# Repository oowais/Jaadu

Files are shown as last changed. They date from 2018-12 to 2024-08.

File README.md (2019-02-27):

# Jaadu : the Alien in FabTerrarium

A **FabTerrarium** is a space with different animals/plants which can interact with users or other entities within the terrarium. These animals/plants are either 3D prninted or soft-robots or a combination of both.

**Jaadu** is an alien in the FabTerrarium who is curious about the different animals or plants in the space. It is a small toddler who crawls in the terrarium reading the emotions of the other entities and displaying those emotions in itself.

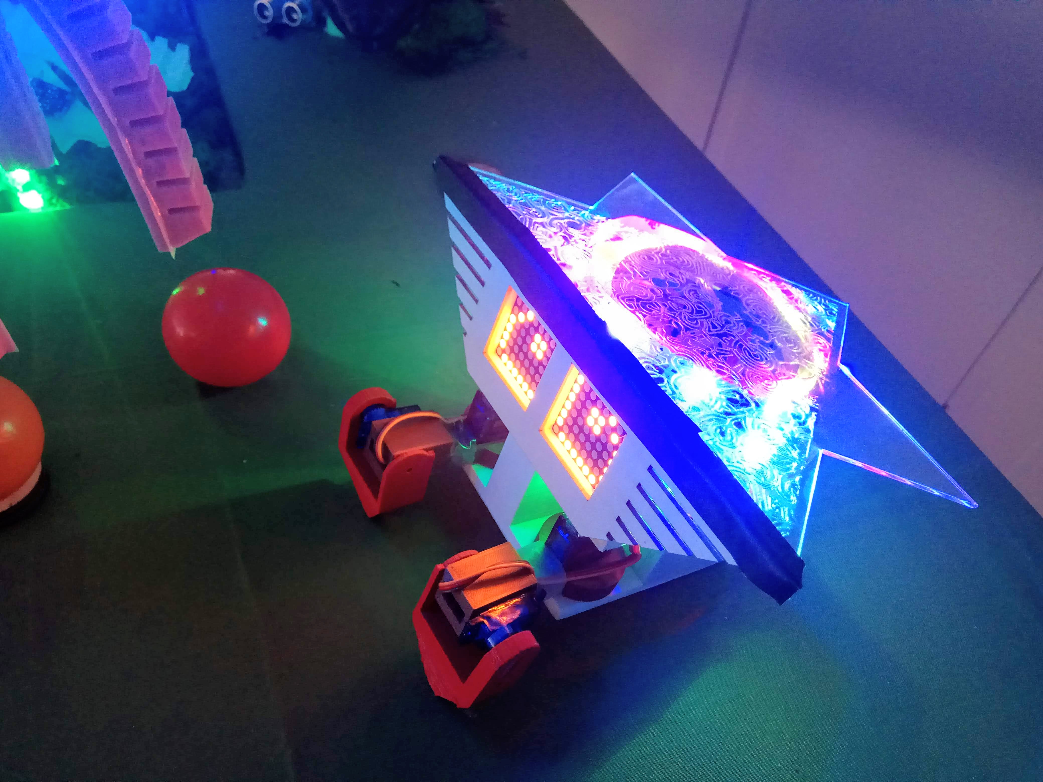
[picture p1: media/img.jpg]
Jaadu


**PowerHand** is the movement controller for the Alien. Moving it around triggers the Alien to move.

**Emotion Gateways** are the gateways placed in the Terrarium through which the Alien can pick up emotions of other entities.

Read more at our [blog](https://students.hci.rwth-aachen.de/category/ws1819/mcp-ws1819-group2) on the project and how it came to be.

## Repo Details

* **alien** : Contains the code for the Alien.
* **backdoor** : Contains the client side code for communicating with the backdoor over MQTT.
* **ground** : Contains the code for synchronization between the Emotion Gateways and sending the triggers in the ground to the Alien.
* **media** : Different images/videos used in the repo.
* **models** : All models designed for laser cutting or 3D printing, some discarded and some used.
* **powerhand** : Code for control of LEDs and triggers sent to Alien in the PowerHand.
* **scripts** : Contains scripts used in the project.
* **testing_modules** : Testing codes and information.

## Items used

* **Alien :**
  * RasPI Zero W
  * Adafruit RGB LED Strip
  * Adafruit LED 8x8 Matrix (2)
  * TowerPro SG90 Servo (4)
* **PowerHand :**
  * Arduino Nano
  * Accelerometer
  * HC-05 Bluetooth Module
  * Adafruit RGB LED Strip
* **Ground :**
  * Arduno Uno
  * HC-05 Bluetooth Module
  * HC-SR04 Ultrasonic Sensor (2)
  * Adafruit RGB LED Strip (2)
* **Additionally :**
  * Finnappee
  * PlexiGlas
  * PLA
  * Breadboard
  * Jumper Cables
  * Tapes
  * Loads and loads of Glue

# Thoughts on looking back

* The walking mechanism developed which relies on the Servos is not suitable to be driven by a RasPI. The Servos by TowerPro are not really reliable and go bust often. A better and reliable mechanism is needed.
* Bluetooth HC-05 module keeps disconnecting after some time, not reliable.
* RaspPi Zero W with it's single core is not a good driver for 7 threads. Things get real slow real quick. RasPI 3 might be a better alternative.
* PowerHand doesn't have proper signifiers for how to use it. Design could be better.
* Power requirements for the LED Matrix, LED Strip is quite high. A 1.5A current (given out usually a small powerbank) is not sufficient. A smaller, light-weight and higher output current power source should be thought of.

---

The **Interactive FabTerrarium** project was conducted as the **Media Computing Project** by the [Media Computing Group](https://hci.rwth-aachen.de/) group under [RWTH Aachen](http://www.rwth-aachen.de).

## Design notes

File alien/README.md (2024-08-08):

# Alien

The central controller for all the different individual components inside the Alien.

## Wiring

**Note :** Servos are driven by external power (RasPI can't bear the load). All VCC and GND for Servos need to be connected to the external source. External power source GND also has to be connected with RasPI GND.

<table>
  <tr>
    <th> Connection </th><th> Right </th><th> RasPI Zero W Board </th><th> Left </th><th> Connection </th>
  </tr>
  <tr>
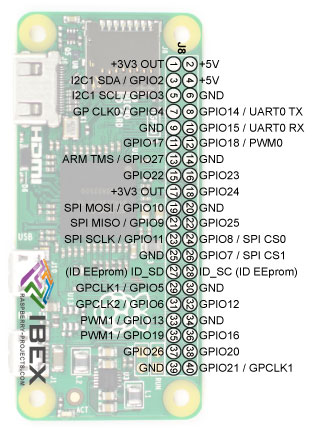
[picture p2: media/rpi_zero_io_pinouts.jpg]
    <td></td><td>1</td><td rowspan=20>  </td> <td>2</td><td>VCC OUT</td>
  </tr>
  <tr>
    <td>Left Eye SDA</td><td>3</td><td>4</td><td></td>
  </tr>
  <tr>
    <td>Left Eye SCL</td><td>5</td><td>6</td><td>GND OUT</td>
  </tr>
  <tr>
    <td></td><td>7</td><td>8</td><td></td>
  </tr>
  <tr>
    <td></td><td>9</td><td>10</td><td></td>
  </tr>
  <tr>
    <td></td><td>11</td><td>12</td><td>LED DOUT</td>
  </tr>
  <tr>
    <td></td><td>13</td><td>14</td><td></td>
  </tr>
  <tr>
    <td></td><td>15</td><td>16</td><td>Right Eye SDA</td>
  </tr>
  <tr>
    <td></td><td>17</td><td>18</td><td>Right Eye SCL</td>
  </tr>
  <tr>
    <td></td><td>19</td><td>20</td><td></td>
  </tr>
  <tr>
    <td></td><td>21</td><td>22</td><td>Right Leg CTRL</td>
  </tr>
  <tr>
    <td></td><td>23</td><td>24</td><td></td>
  </tr>
  <tr>
    <td>GND for External Power</td><td>25</td><td>26</td><td></td>
  </tr>
  <tr>
    <td></td><td>27</td><td>28</td><td></td>
  </tr>
  <tr>
    <td></td><td>29</td><td>30</td><td>GND OUT</td>
  </tr>
  <tr>
    <td></td><td>31</td><td>32</td><td></td>
  </tr>
  <tr>
    <td></td><td>33</td><td>34</td><td></td>
  </tr>
  <tr>
    <td></td><td>35</td><td>36</td><td>Left Leg CTRL</td>
  </tr>
  <tr>
    <td>Right Foot CTRL</td><td>37</td><td>38</td><td>Left Foot CTRL</td>
  </tr>
  <tr>
    <td></td><td>39</td><td>40</td><td></td>
  </tr>
</table>

## Installation

Run the [script](../scripts/) to complete installation of the alien package inside RasPI.
Starts the Alien program automatically as a service on the RasPI.

## Some things to take care

Changes in **lib/globals.py** :

* **EXTERNAL_BROKER_HOST** needs to point to the IP address of the MQTT Broker.
* **EXTERNAL_BROKER_PORT** needs to be changed if the Broker listens at a different port (1883 is default)
* **WALKING_PINS** are RasPI GPIO pin numbers and need to be changed if the connection is made different from as given.
* **MOVE_CONTROL_VALUES** are experimental values. The exact values change depending on how the Alien legs are screwed in.
Experiments can be done using [this](../testing_modules/pigpio_test/servo_demo.py).
* **WALKING_PINS** has GPIO pin numbers. Need to be changed if using different connection.
* **HAND_BLUETOOTH_MAC** according to the MAC of the powerhand Bluetooth device.
* **GROUND_BLUETOOTH_MAC** according to the MAC of the ground connected Bluetooth device.
* **LED_STRIP_PIN** is the GPIO pin number. Change if using different connections.
* **NUM_PIXELS_USED** change according to number of LEDs in the strip used in Alien.

Changes in **mqtt_topic_mappings.json** :

Change the topic on which the emotions are sent by the other entities in the terrarium and unique key we will be using to track those emotions.

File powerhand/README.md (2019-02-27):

## Powerhand

**PowerHand** is the movement controller for the Jaadu. Moving it around triggers the Jaadu to move.

By pressing the button and moving the the powerhand in specific directions, can move Jaadu forward, left and right. Using a gesture via powerhand Jaadu can also say Hi.

[Link to demo video](https://www.youtube.com/watch?v=woAhQqzkfWM)

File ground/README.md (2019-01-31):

# Ground Controller

Arduino code used to receive triggers from the Gateways and signal via Bluetooth to the main Alien. The Alien receives the trigger and translates the emotion for the entity in the terrarium corresponding to the Gateway.

Each Gateway has a __LED Strip__ (breathing lights showing Gateway state) and an __UltraSonic sensor__.

## Wiring
* As defined in the [code](./ground.ino)
* For Bluetooth :
  * RX (on bluetooth) :arrow_right: tx_conn (on Arduino)
  * TX (on bluetooth) :arrow_right: rx_conn (on Arduino)
  * VCC connected to 3.3V OUT.

## Gateway States

* __Neutral :__ None of the Gateways are activated. LED Strips display BLUE color.
* __Activated :__  The UltraSonic sensor is triggered when some obstruction is detected in front of the gateway. (10-16 cms range). The LED Strips corresponding to the Gateway turn into GREEN color.
* __Deactivated :__ When one gateway is activated, others are in this state and doesn't trigger even when some object comes in the activation range. The LED Strips corresponding to the Gateway display RED color.

## Before Using

* If Pins used are different than given then have to change the corresponding pin numbers in **ground.ino**
* Each Gateway instance needs a separate character to be provided as uniqueID. These characters should correspond to triggers in the [receiver code](../alien/lib/ground_coordinator.py)

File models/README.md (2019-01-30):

# Models

All the STL (for 3D printing) and SVG (for Laser cutting) files developed for the project.

## Alien

* **arm_left :** Left Leg for the Alien
* **arm_right :** Right Leg for the Alien
* **backmost_hold :** A back stand for the alien, although we ended up making it using plexiglas which can be found in the backmost_glass.
* **base :** The complete base on which the other components are glued in. Contains holes to fit the Alien Legs.
* **finishing :** Some finishing parts for the Alien. Like the Face mask, the top gear of the Alien.
* **front :** The eye sockets for the Alien's face.
* **leg_left :** Left foot for the Alien.
* **leg_right :** Right foot for the Alien.
* **rasp_case :** A case to keep the RasPI (not really required, can be removed or better to screw in RasPI).
* **body :** The complete Alien look for visualization purpose. (without the finishing)

## Ground

* **middle_part :** The middle hold for the Gateway. Around the curved stripes LED strips are put.
* **sonar_cut :** A piece of material, which is used for the decoration of the UltraSonic sensor.
* **talk_points :** The complete gateway assembled look for visualization.

## Powerhand

* **battery_holder :** Hollow case for holding a standard sized 9V barrel battery.
* **button_holder :** To hide exposed wires going from button. button_holder_1 not really useful.
* **extension_holder :** The holder to insert the extensions in.
* **extension :** Extensions which are used for decorative purpose.
* **powerhand :** The complete powerhand assembled look for visualization.

## Discarded

A lot of models went through different design phases in the DIA cycle.
Many were discarded either due to lack of usability or not suited for our end product.
All these models dumps are available here, although they are not ordered or maintained in a proper fashion.

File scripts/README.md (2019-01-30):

# One-click setup

Script to completely setup a vanilla RasPI to run the codebase.

**Note :** Written for **Raspbian Stretch Lite (version November 2018)**.

#### Before using

* Make sure there is active internet connection in the RasPI
* Connect the Eyes (LED Matrix) to the proper pins in the RasPI since the I2C address is fetched by the script.
If eye is not connected, update the I2C address later by doing the following :
  * `i2cdetect -y 1`
  * Get the address displayed in the Matrix. If address is 0x70 nothing more needs to be done.
  * If address is something else, modify EYE_I2C_ADDRESS in [globals.py](../alien/lib/globals.py)
* If you wish to use backdoor, the set it up when asked by the script. Know more about backdoor [here](../backdoor/)

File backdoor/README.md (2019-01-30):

# Alien Backdoor

A direct secure command stream between Alien and an admin. Can be used to remotely trigger event-based triggers manually.

To be used for demo purposes (only) or to play God with the Alien (maybe?).

Needs a MQTT broker to be already setup which can relay the commands.

#### Before using

* Make sure you are in the same network as your MQTT Broker, and modify __connect.json__ to point to it.
* `pip3 install -r requirements.txt`

---

### Can anyone now send commands to Alien?

Ofcourse not, that would make it an open field for anyone to mess with the Alien at any point of time.

Credentials need to be setup during the [installation](../scripts/install-raspi.sh) of the RasPI to allow backdoor functionality.

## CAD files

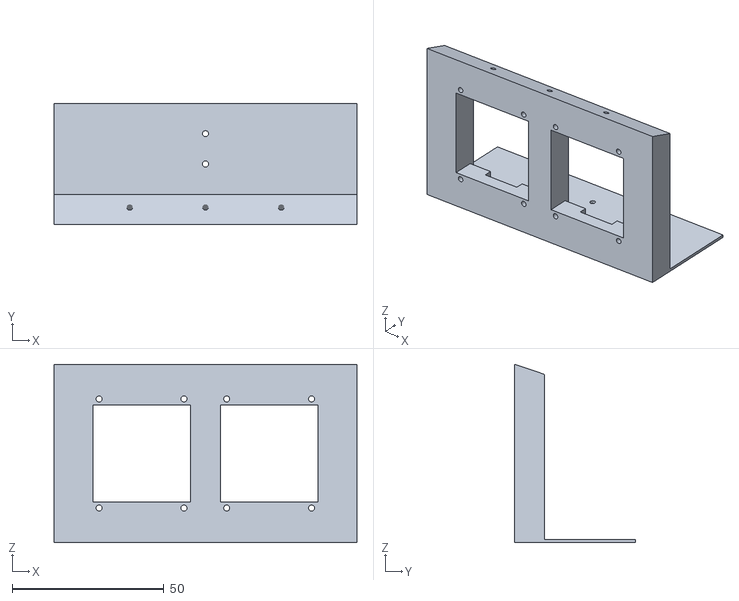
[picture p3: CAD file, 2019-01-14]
models/alien/stl/front.stl
100.0 x 40.0 x 58.9

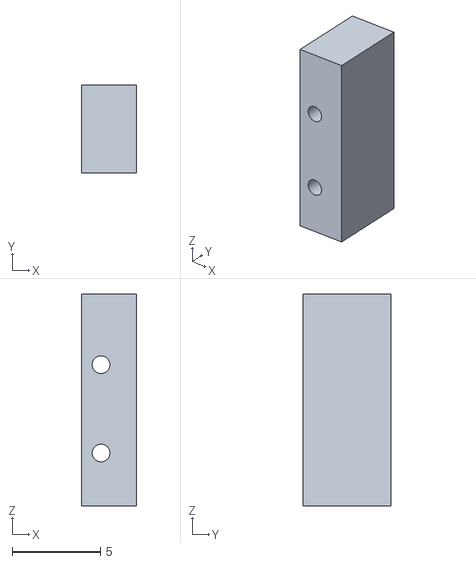
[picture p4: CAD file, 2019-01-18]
models/powerhand/stl/button_holder_1.stl
3.10 x 5.00 x 12.0

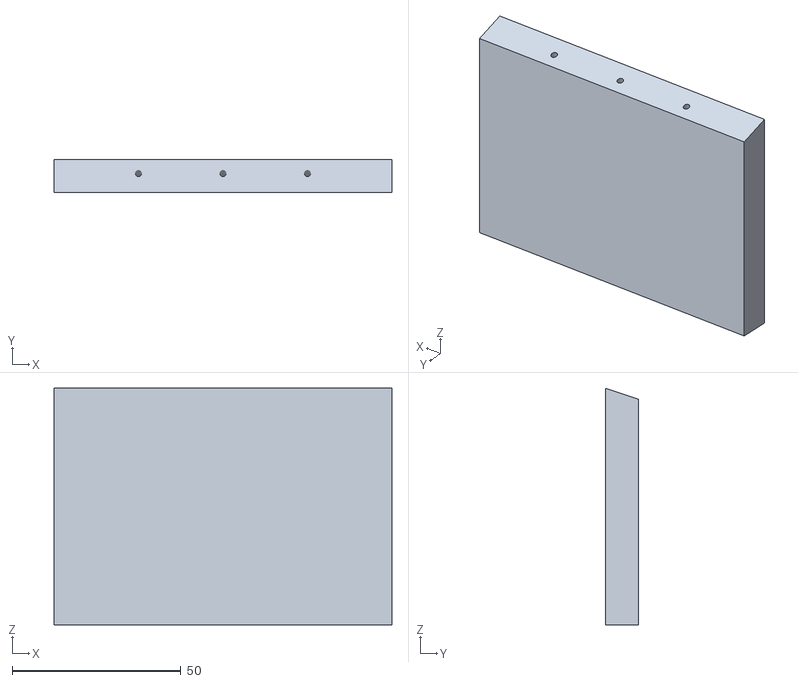
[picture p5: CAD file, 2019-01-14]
models/alien/stl/backmost_hold.stl
100.0 x 9.80 x 70.0

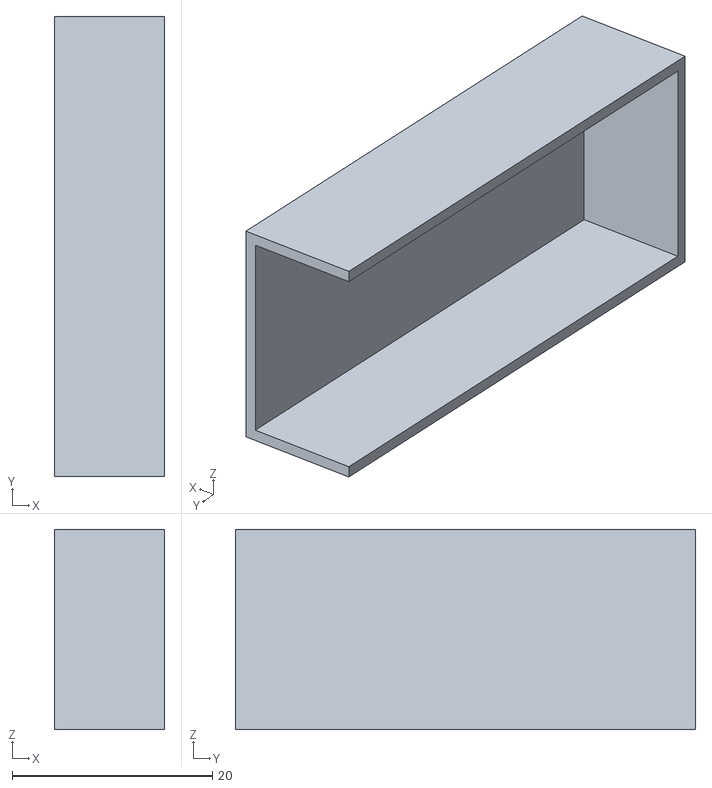
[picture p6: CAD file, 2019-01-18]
models/powerhand/stl/bluetooth_holder.stl
11.0 x 46.0 x 20.0

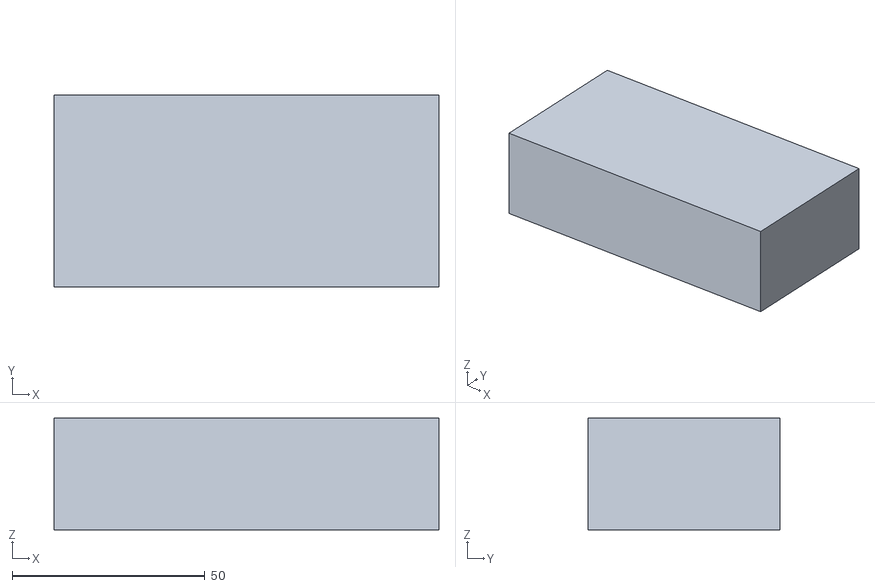
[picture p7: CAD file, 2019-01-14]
models/alien/stl/battery_holder.stl
100.0 x 50.0 x 29.0

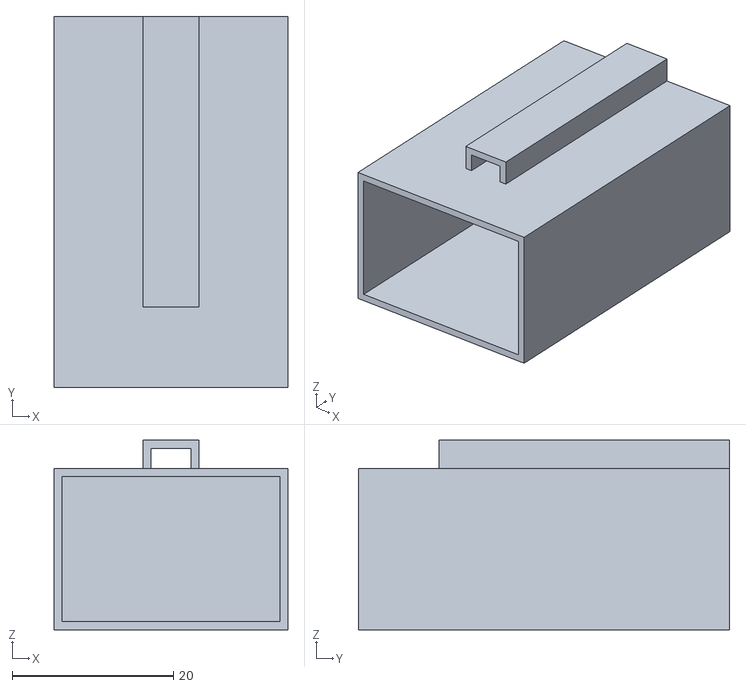
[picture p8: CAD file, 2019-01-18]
models/powerhand/stl/battery_holder.stl
29.0 x 46.0 x 23.5

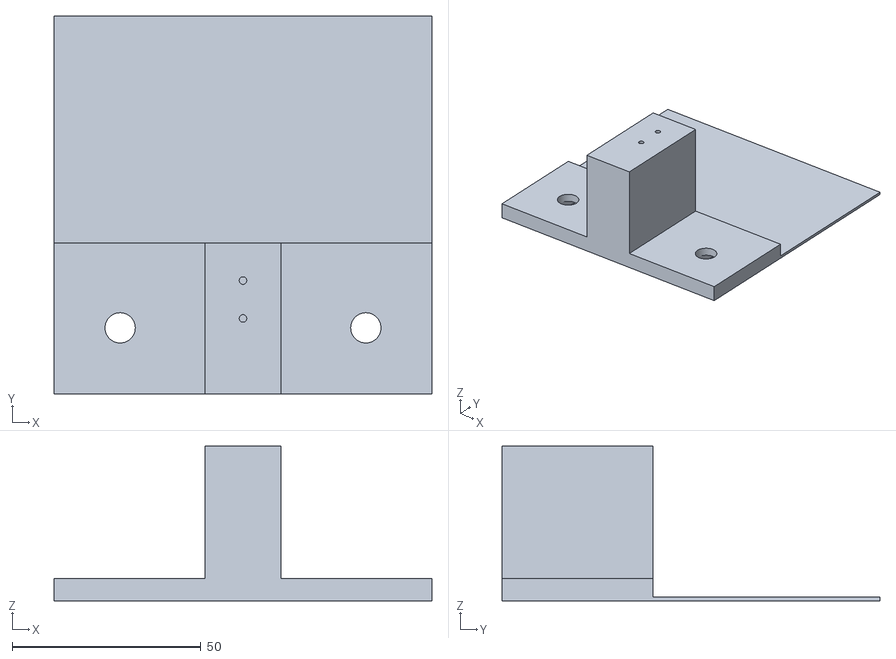
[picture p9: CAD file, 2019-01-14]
models/alien/stl/base.stl
100.0 x 100.0 x 41.0

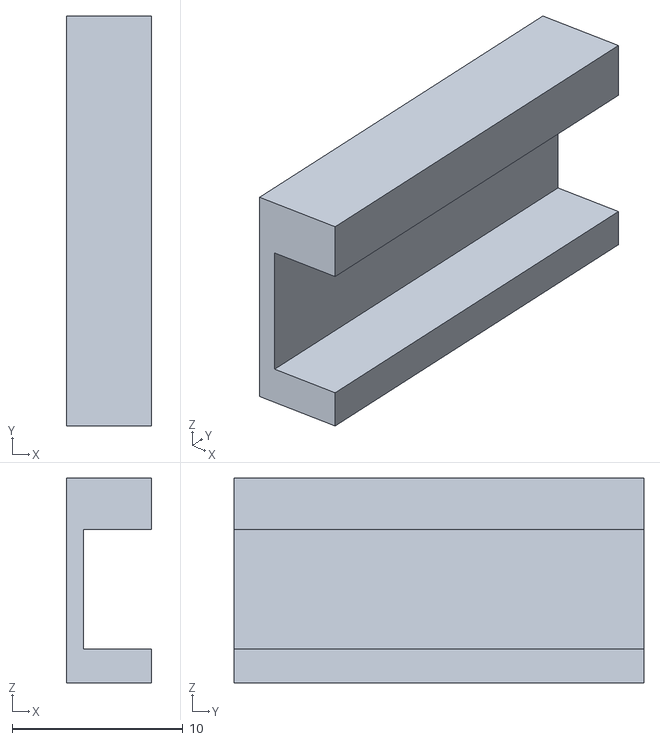
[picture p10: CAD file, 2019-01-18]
models/powerhand/stl/button_holder_2.stl
5.00 x 24.0 x 12.0

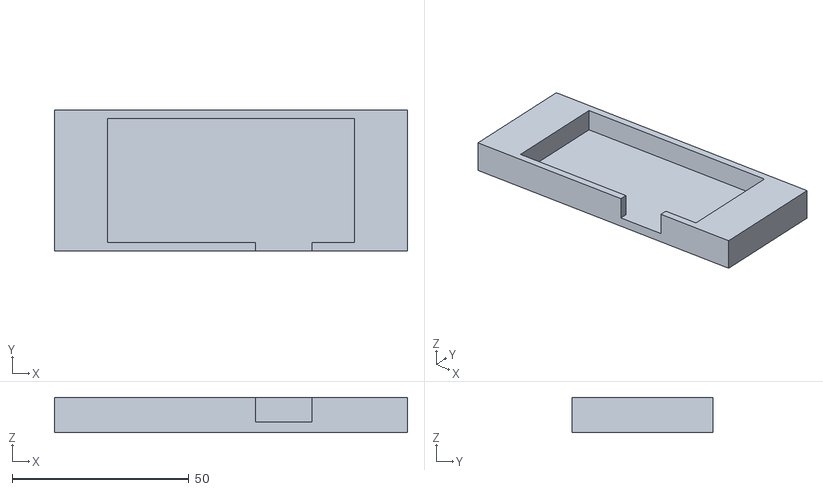
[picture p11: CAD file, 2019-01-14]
models/alien/stl/rasp_case.stl
100.0 x 40.0 x 10.0

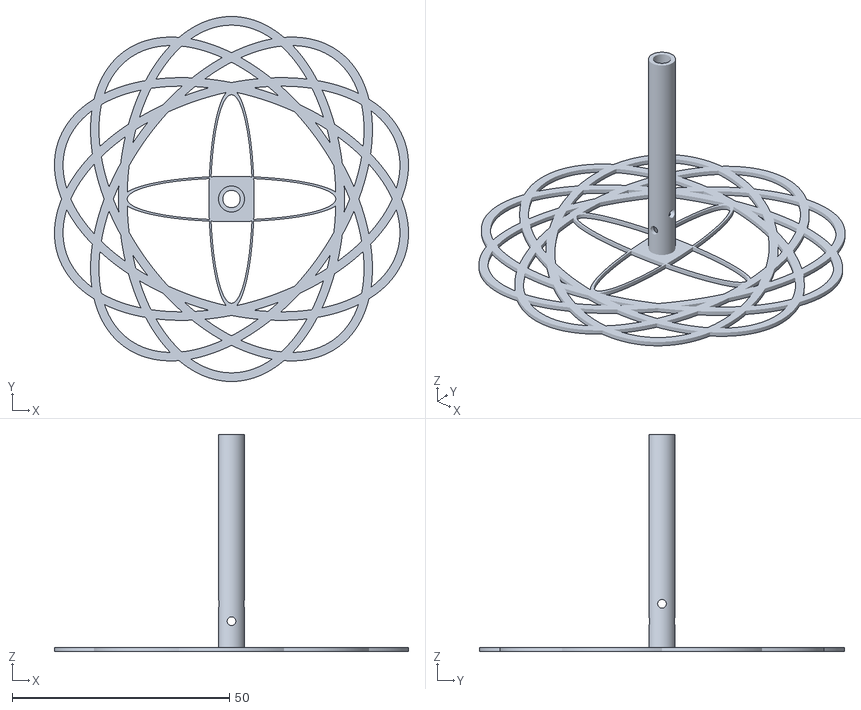
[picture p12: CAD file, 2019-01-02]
models/alien/stl/arc_reactor.stl
81.5 x 84.0 x 50.0

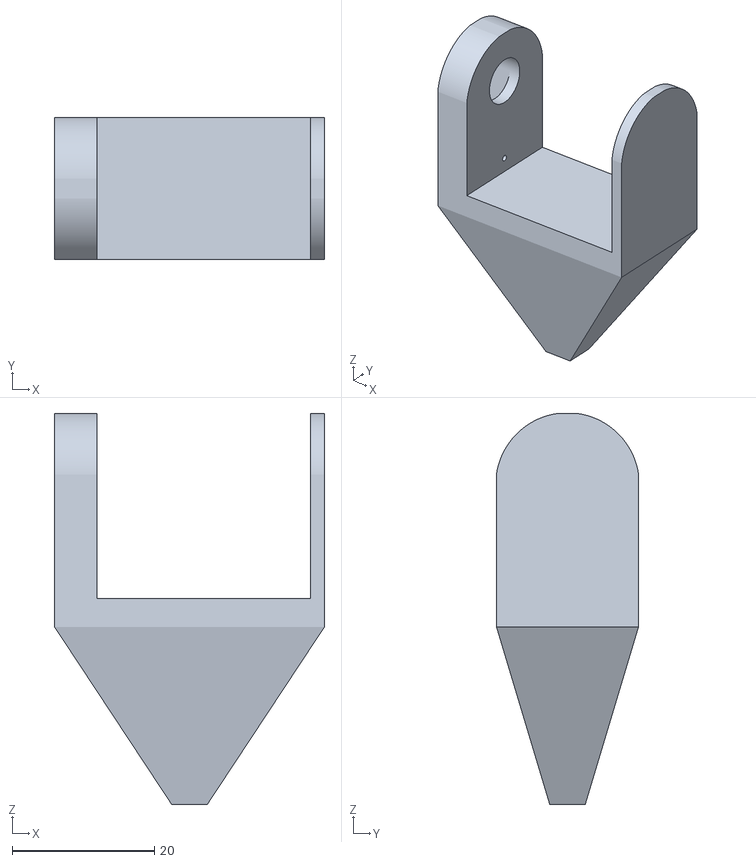
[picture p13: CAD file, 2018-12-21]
models/alien/stl/leg_left.stl
38.0 x 20.0 x 55.0

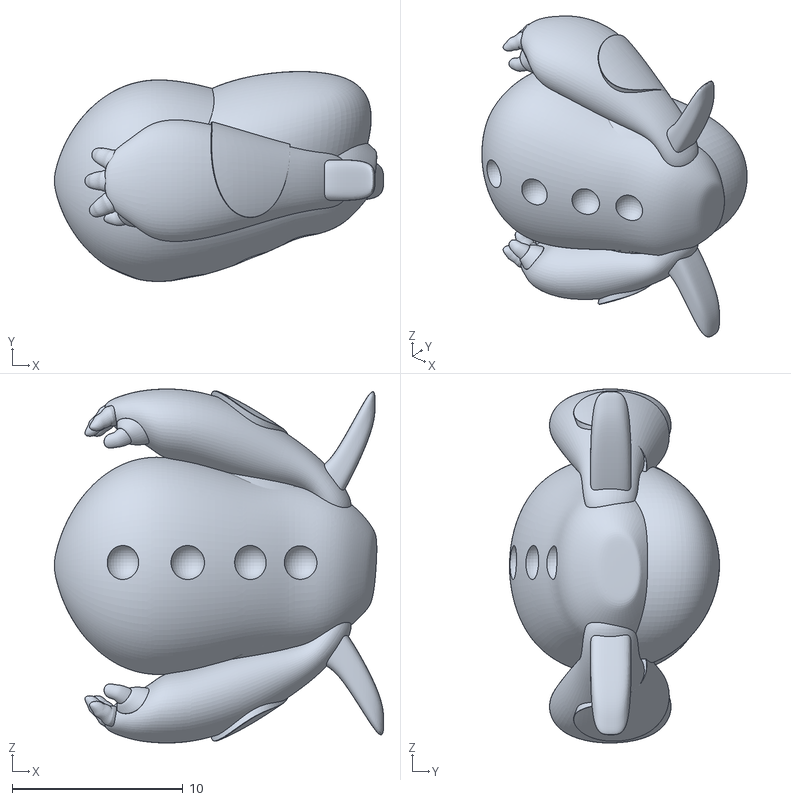
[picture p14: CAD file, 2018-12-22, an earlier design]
models/discarded/alien-v1/Body.stl
19.3 x 12.3 x 20.7

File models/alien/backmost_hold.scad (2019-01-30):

include <globals.scad>

module backmost_hold(x, y, z) {
    difference() {
        cube([x, y, z]);
        for (i = [2.5: 2.5: x-2.5]) {
            translate([i, 0.3, z-1]) rotate([-lower_elevation_deg, 0, 0]) cylinder(r=screw_r, h=1);
        }
    }
}

module backmost_glass(front_z, back_z) {
  // Have to make about 24 pieces of it to fill up backmost_hold 
  hull() {
      cube([0.2, 0.1, back_z]);
      translate([0, 0.8, 0]) cube([0.2, 0.1, front_z]);
  }  
}

$fn=300;
scale([10, 10, 10]) backmost_hold(x=total_x, y=bp_total_y, z=bp_total_z);
//scale([10, 10, 10]) rotate([0, 90, 0]) backmost_glass(front_z=6.5, back_z=6.7);

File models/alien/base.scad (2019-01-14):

include <globals.scad>

module base(x, y, z) {
    difference() {
        union() {
            cube([x, y, b_overall_z]);
            cube([x, b_legspace, b_legfit_z]);
            translate([b_legspace, 0, b_legfit_z]) cube([x-(b_legspace*2), b_legspace, z-b_legfit_z]);
        }
        translate([(l_arms_base_d/2), (l_arms_base_d/2), -0.01]) linear_extrude(height=1, $fn=300) circle(r=0.4);
        hull() {
            translate([(l_arms_base_d/2), (l_arms_base_d/2), -0.01]) linear_extrude(height=0.31, $fn=300) circle(r=0.4);
            translate([(l_arms_base_d/2), (l_arms_base_d/2)+1.5, -0.01]) linear_extrude(height=0.31, $fn=300) circle(r=0.2);
        } 
        
        translate([x-(l_arms_base_d/2), (l_arms_base_d/2), -0.01]) linear_extrude(height=1, $fn=300) circle(r=0.4); 
        hull() {
            translate([x-(l_arms_base_d/2), (l_arms_base_d/2), -0.01]) linear_extrude(height=0.31, $fn=300) circle(r=0.4);
            translate([x-(l_arms_base_d/2), (l_arms_base_d/2)+1.5, -0.01]) linear_extrude(height=0.31, $fn=300) circle(r=0.2);
        } 
        
        translate([x/2, base_head_fit_1, z-screw_h]) cylinder(r=screw_r, h=3);
        translate([x/2, base_head_fit_2, z-screw_h]) cylinder(r=screw_r, h=3);
    }
}

$fn=300;
scale([10, 10, 10]) base(x=total_x, y=total_y, z=base_total_z);

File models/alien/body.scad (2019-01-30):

include <globals.scad>
use <rasp_case.scad>
use <front.scad>
use <base.scad>
use <backmost_hold.scad>
use <arm_right.scad>
use <arm_left.scad>
use <leg_right.scad>
use <leg_left.scad>

module total_body(x, y, z) {
    base(x=x, y=y, z=base_total_z);
    translate([0, 0, base_total_z + filler]) {
        front(x=x, y=face_total_y, z=face_total_z);
    }
    
    translate([0, b_legspace + filler + (bh_y - raspi_total_y), b_overall_z + filler]) {
        raspi_case(x=x, y=raspi_total_y, z=raspi_total_z);
    }
    
    translate([0, b_legspace + filler + bh_y + filler, b_overall_z + filler]) {
        backmost_hold(x=total_x, y=bp_total_y, z=bp_total_z);
    }
    
    translate([9.15, -4.3, b_legfit_z + filler]) arm_left();
    translate([0.85, -4.3, b_legfit_z + filler]) arm_right();
    translate([10, -4, -3.2]) rotate([9, 0, 0]) leg_left();
    translate([0, -4, -3.2]) rotate([9, 0, 0]) leg_right();
}

$fn=300;
translate([-5, 0, 2.2]) rotate([-elevation_deg, 0, 0]) total_body(x=total_x, y=total_y, z=total_z);

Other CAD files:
models/alien/stl/leg_right.stl
models/alien/finishing.scad
models/alien/front.scad
models/alien/globals.scad
models/alien/rasp_case.scad
models/discarded/alien-v2/arc_cup_holder.scad
models/discarded/alien-v2/arc_reactor.scad
models/discarded/alien-v2/arc_reactor_cup.scad
models/discarded/alien-v2/arm_left.scad
models/discarded/alien-v2/arm_right.scad
models/discarded/alien-v2/body.scad
models/discarded/alien-v2/body_back.scad
models/discarded/alien-v2/body_front.scad
models/discarded/alien-v2/down_holder.scad
models/discarded/alien-v2/down_holder_2.scad
models/discarded/alien-v2/head.scad
models/discarded/alien-v2/head_back_holder.scad
models/discarded/alien-v2/head_front_holder.scad
models/discarded/alien-v2/leg_left.scad
models/discarded/alien-v2/leg_right.scad
models/discarded/alien-v2/neck_holder.scad
models/discarded/alien-v2/top.scad
models/discarded/alien-v3/battery_holder.scad
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

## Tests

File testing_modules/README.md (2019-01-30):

# Testing code for Modules

Multiple modules were individually tested and coded before integrating into the main framework.
All modules and their sample/prototype codes are available in this directory.

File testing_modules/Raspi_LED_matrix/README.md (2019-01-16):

## Prerequisites
Enable i2c and spi interface(if required) in raspi-config from [here](https://learn.adafruit.com/adafruits-raspberry-pi-lesson-4-gpio-setup/configuring-i2c)

> spi not required for Adafruit library(as of now).

Then install the following:
`sudo apt-get install -y python-smbus`
`sudo apt-get install -y i2c-tools`

Test if i2c is enabled or not  
`sudo i2cdetect -y 1`

Test if spi interface  
`ls -l /dev/spidev*`

> Should see 2 devices

## Using Adafruit library to use Adafruit backpack
[Github Link](https://github.com/adafruit/Adafruit_Python_LED_Backpack)
```
sudo apt-get update
sudo apt-get install -y git build-essential python3-dev python3-smbus python-imaging python3-pip python3-pil

git clone https://github.com/adafruit/Adafruit_Python_LED_Backpack.git
cd Adafruit_Python_LED_Backpack
sudo python3 setup.py install
```
Then run eye.py using  
sudo python3 eye.py

> More eye expression to be added.

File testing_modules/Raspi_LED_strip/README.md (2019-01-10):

## Requirements

sudo pip3 install rpi_ws281x adafruit-circuitpython-neopixel

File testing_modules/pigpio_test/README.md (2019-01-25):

### Install pigpio library
```
wget abyz.me.uk/rpi/pigpio/pigpio.zip
unzip pigpio.zip
cd PIGPIO
make
sudo make install
```

#### Start the pigpio daemon
sudo pigpiod

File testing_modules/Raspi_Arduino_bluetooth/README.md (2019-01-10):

# pybluez installation
sudo apt-get install bluetooth libbluetooth-dev
sudo python3 -m pip install pybluez

# Ignore the below things, they are a part of old testing

# nothing happened with this i guess: sudo apt-get install -y bluez-obexd
# bluetooth control commands to connect to a new device
sudo bluetoothctl # use of sudo is must
agent on
pairable on
scan on
# find the BT thing you want, copy its address
scan off
pair <physical-addr>
# input pin
trust <physical-addr>
connect <physical-addr>
exit

# after restart
echo -e "connect 98:D3:31:F5:B9:E7\nquit" | bluetoothctl

# installing bluez in raspi
wget http://www.kernel.org/pub/linux/bluetooth/bluez-5.49.tar.xz
tar xvf bluez-5.49.tar.xz
cd bluez-5.49
./configure
        # for dependency errors: 
        sudo apt-get install libglib2.0-dev libdbus-1-dev libudev-dev libical-dev libreadline-dev
make
sudo make install
sudo reboot

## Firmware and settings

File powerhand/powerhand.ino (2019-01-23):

#include <SoftwareSerial.h>
#include <Adafruit_NeoPixel.h>
#ifdef __AVR__
#include <avr/power.h>
#endif

#define PIN 10
/*
  The circuit:
  - analog 7: z-axis
  - analog 6: y-axis
  - analog 5: x-axis
  Possble Case-
  - analog 0/GND: VCC
  - analog 4/5V: GND
*/

/*
  Wires:
  Red: A4/VCC
  Grey: A0/GND
  Yellow: X_OUT A3
  Purple: Y_OUT A2
  Orange: Z_OUT A1

*/
Adafruit_NeoPixel strip = Adafruit_NeoPixel(18, PIN, NEO_GRB + NEO_KHZ800);
SoftwareSerial bt (5, 6);
char expression;
char motion;

const int buttonPin = 9;
const int groundpin = A0;
const int powerpin = A4;
const int zPin = A1;
const int yPin = A2;
const int xPin = A3;

const uint32_t lemon = strip.Color(255, 165, 0); //surprise
const uint32_t red = strip.Color(255, 0, 0); //angry
const uint32_t green = strip.Color(0, 255, 0); //happy
const uint32_t blue = strip.Color(0, 0, 255); //sad
const uint32_t greenishBlue = strip.Color(0, 127, 34); //sending data
const uint32_t cyan = strip.Color(0, 255, 255); //sleepy
const uint32_t off = strip.Color(0, 0, 0);

int xInit;
int yInit;
int zInit;

int xRead;
int yRead;
int zRead;

int buttonState = 0;

void setup() {
  pinMode(groundpin, OUTPUT);
  pinMode(powerpin, OUTPUT);
  pinMode(buttonPin, INPUT);
  digitalWrite(groundpin, LOW);
  digitalWrite(powerpin, HIGH);

  strip.begin();
  strip.show();

  bt.begin(9600);
  Serial.begin(9600);
  Serial.print("Bluetooth ON!");
}

void loop() {
  buttonState = digitalRead(buttonPin);
  while (buttonState == LOW) {
    motion = getDataFromGyro();
    if (motion != 's') {
      sendDataToRaspi(motion);
      Serial.println(motion);
    }

    if (motion == 'l')
      leftLed(greenishBlue, 50);
    else if (motion == 'r')
      rightLed(greenishBlue, 50);
    else if (motion == 'f' or motion =='u')
      blinkLed(greenishBlue, 100);
    clearStrip();
    delay(300);
    buttonState = digitalRead(buttonPin);
    if (buttonState == HIGH) {
      sendDataToRaspi('x');
    }
  }
  if (buttonState == HIGH) {
    rainbow(30);
    //getExpressionFromRaspiNShow();
  }
  delay(50);
}

char getDataFromGyro() {
  char data = 's';
  xRead = analogRead(xPin);
  yRead = analogRead(yPin);
  zRead = analogRead(zPin);

  //if (zRead < 330) //Hand face up
  //else if (zRead > 400) //Hand face down

  if (xRead > 320 && xRead < 380 && yRead > 310 && yRead < 380) //stop
    data = 's';

  else {
    if (yRead >= 380) //Forward
      data = 'f';
    else if (yRead <= 310)
      data = 'u'; //Back, get expression from Squid

    if (xRead <= 320) //Left
      data = 'l';
    else if (xRead >= 380) //Right
      data = 'r';
  }
  return data;
}

void sendDataToRaspi(char data) {
  bt.print(data);
}

void blinkLed(uint32_t c, uint8_t wait) {
  for (uint16_t i = 0; i < strip.numPixels(); i++) {
    strip.setPixelColor(i, c);
  }
  strip.show();
  delay(wait);

  for (uint16_t i = 0; i < strip.numPixels(); i++) {
    strip.setPixelColor(i, off);
  }
  strip.show();
  delay(wait);
}

void leftLed(uint32_t c, uint8_t wait) {
  strip.setPixelColor(9, c);
  strip.setPixelColor(8, c);
  strip.show();
  delay(wait);

  strip.setPixelColor(9, off);
  strip.setPixelColor(8, off);
  strip.setPixelColor(10, c);
  strip.setPixelColor(7, c);
  strip.show();
  delay(wait);

  strip.setPixelColor(10, off);
  strip.setPixelColor(7, off);
  strip.setPixelColor(11, c);
  strip.setPixelColor(6, c);
  strip.show();
  delay(wait);

  strip.setPixelColor(11, off);
  strip.setPixelColor(6, off);
  strip.setPixelColor(12, c);
  strip.setPixelColor(5, c);
  strip.setPixelColor(0, c);
  strip.show();
  delay(wait);

  strip.setPixelColor(12, off);
  strip.setPixelColor(5, off);
  strip.setPixelColor(0, off);
  strip.setPixelColor(13, c);
  strip.setPixelColor(4, c);
  strip.setPixelColor(1, c);
  strip.show();
  delay(wait);

  strip.setPixelColor(13, off);
  strip.setPixelColor(4, off);
  strip.setPixelColor(1, off);
  strip.setPixelColor(14, c);
  strip.setPixelColor(3, c);
  strip.setPixelColor(2, c);
  strip.show();
  delay(wait);

  strip.setPixelColor(14, off);
  strip.setPixelColor(3, off);
  strip.setPixelColor(2, off);
  strip.setPixelColor(15, c);
  strip.show();
  delay(wait);

  strip.setPixelColor(15, off);
  strip.setPixelColor(16, c);
  strip.show();
  delay(wait);

  strip.setPixelColor(16, off);
  strip.setPixelColor(17, c);
  strip.show();
  delay(wait);

  strip.setPixelColor(16, off);
  strip.setPixelColor(17, c);
  strip.show();
  delay(wait);
  strip.setPixelColor(17, off);
  strip.show();
}

void rightLed(uint32_t c, uint8_t wait) {
  strip.setPixelColor(17, c);
  strip.show();
  delay(wait);

  strip.setPixelColor(17, off);
  strip.setPixelColor(16, c);
  strip.show();
  delay(wait);

  strip.setPixelColor(16, off);
  strip.setPixelColor(15, c);
  strip.show();
  delay(wait);

  strip.setPixelColor(15, off);
  strip.setPixelColor(14, c);
  strip.setPixelColor(3, c);
  strip.setPixelColor(2, c);
  strip.show();
  delay(wait);

  strip.setPixelColor(14, off);
  strip.setPixelColor(3, off);
  strip.setPixelColor(2, off);
  strip.setPixelColor(13, c);
  strip.setPixelColor(4, c);
  strip.setPixelColor(1, c);
  strip.show();
  delay(wait);

  strip.setPixelColor(13, off);
  strip.setPixelColor(4, off);
  strip.setPixelColor(1, off);
  strip.setPixelColor(12, c);
  strip.setPixelColor(5, c);
  strip.setPixelColor(0, c);
  strip.show();
  delay(wait);

  strip.setPixelColor(12, off);
  strip.setPixelColor(5, off);
  strip.setPixelColor(0, off);
  strip.setPixelColor(11, c);
  strip.setPixelColor(6, c);
  strip.show();
  delay(wait);

  strip.setPixelColor(11, off);
  strip.setPixelColor(6, off);
  strip.setPixelColor(10, c);
  strip.setPixelColor(7, c);
  strip.show();
  delay(wait);

  strip.setPixelColor(10, off);
  strip.setPixelColor(7, off);
  strip.setPixelColor(9, c);
  strip.setPixelColor(8, c);
  strip.show();
  delay(wait);

  strip.setPixelColor(9, off);
  strip.setPixelColor(8, off);
  strip.show();
}

void leftLedTop(uint32_t c, uint8_t wait) {
  for (uint16_t i = 9; i < 18; i++) {
    if (i > 9)
      strip.setPixelColor(i - 1, off);
    strip.setPixelColor(i, c);
    strip.show();
    delay(wait);
  }
}

void rightLedTop(uint32_t c, uint8_t wait) {
  for (uint16_t i = 17; i > 8; i--) {
    if (i < 17)
      strip.setPixelColor(i + 1, off);
    strip.setPixelColor(i, c);
    strip.show();
    delay(wait);
  }
}

void rainbow(uint8_t wait) {
  uint16_t i, j;

  for (j = 0; j < 256; j++) {
    for (i = 0; i < strip.numPixels(); i++) {
      strip.setPixelColor(i, Wheel((i + j) & 255));
      buttonState = digitalRead(buttonPin);
      if (buttonState == LOW)
        return;
    }
    strip.show();
    delay(wait);
  }
}

void getExpressionFromRaspiNShow() {
  if (bt.available()) {
    expression = bt.read();
    if (expression == 'h')
      //Serial.println("Happy");
      fill(green);
    else if (expression == 's')
      //Serial.println("Sad");
      fill(blue);
    else if (expression == 'a')
      //Serial.println("Angry");
      fill(red);
    else if (expression == 'z')
      fill(cyan);
    //Serial.println("Sleepy");
    //theaterChaseRainbow(50);
  }
}

void fillOdd(uint32_t c) {
  for (uint16_t i = 1; i < strip.numPixels(); i++) {
    strip.setPixelColor(i, c);
    strip.show();
    i++;
  }
}

void fillEven(uint32_t c) {
  for (uint16_t i = 0; i < strip.numPixels(); i++) {
    strip.setPixelColor(i, c);
    strip.show();
    i++;
  }
}

void clearStrip() {
  for (uint16_t i = 0; i < strip.numPixels(); i++) {
    strip.setPixelColor(i, off);
    strip.show();
  }
}

void fill(uint32_t c) {
  for (uint16_t i = 0; i < strip.numPixels(); i++) {
    strip.setPixelColor(i, c);
    strip.show();
  }
}

// Input a value 0 to 255 to get a color value.
// The colours are a transition r - g - b - back to r.
uint32_t Wheel(byte WheelPos) {
  WheelPos = 255 - WheelPos;
  if (WheelPos < 85) {
    return strip.Color(255 - WheelPos * 3, 0, WheelPos * 3);
  }
  if (WheelPos < 170) {
    WheelPos -= 85;
    return strip.Color(0, WheelPos * 3, 255 - WheelPos * 3);
  }
  WheelPos -= 170;
  return strip.Color(WheelPos * 3, 255 - WheelPos * 3, 0);
}

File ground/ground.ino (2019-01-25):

#include <SoftwareSerial.h>
#include "gateway.h"

// All connections
// Crocodile
byte crocodile_us_trigger = 7;
byte crocodile_us_echo = 8;
byte crocodile_led_din = 9;
// Plant
byte plant_us_trigger = 2;
byte plant_us_echo = 3;
byte plant_led_din = 4;
// Bluetooth
byte rx_conn = 5;
byte tx_conn = 6;

// Gateways to Monitor
Gateway *activatedGateway = NULL;
Gateway *lastWeKnow = NULL;
Gateway crocodile = Gateway('c', crocodile_us_echo, crocodile_us_trigger, crocodile_led_din, 8, &activatedGateway);
Gateway plant = Gateway('p', plant_us_echo, plant_us_trigger, plant_led_din, 8, &activatedGateway);

SoftwareSerial neelaDanth(rx_conn, tx_conn);

void setup() {
  Serial.begin(9600);
  while (!Serial) {;}

  neelaDanth.begin(9600);
  crocodile.setup();
  plant.setup();
}

void loop()
{
  crocodile.getDistanceTrigger();
  plant.getDistanceTrigger();
  crocodile.lightGateway();
  plant.lightGateway();
  if (lastWeKnow != activatedGateway) {
    lastWeKnow = activatedGateway;
    if (&crocodile == activatedGateway) {
      // Send signal for crocodile gate trigger
      neelaDanth.print(crocodile.getUniqueCharID());
    } else if (&plant == activatedGateway) {
      // Send signal for plant gate trigger
      neelaDanth.print(plant.getUniqueCharID());
    } else if (NULL == activatedGateway) {
      // Signifying nothing triggered signal
      neelaDanth.print("x");
    }
  }
}

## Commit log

2018-12-18 Arduino Code
2018-12-19 Base testing of Accelerometer module
2018-12-19 Reconfiguration of projects
    Moved example code from Testing Arduino folder to root and gave projects a common name strucutre
2018-12-21 Adding all available resources
    [arm_left.scad, arm_right.scad, legs_left.scad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]
2018-12-21 Creating separate threads for modules
2018-12-21 Adding old body model
    [Body.stl]
2018-12-27 Alien Body
    [body.scad, body_back.scad, body_front.scad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]
2018-12-27 stl files
    [down_holder.stl, down_holder_2.stl]
2018-12-27 body_front
    STL printed on 27/12
2018-12-27 Create Leg+Accelerometer.ino
    Needs to be tested.
2018-12-27 Moving files around
    [arm_left.scad, arm_right.scad, leg_left.scad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]
2019-01-01 Head Model
    [head.scad, head_back_holder.scad, head_back_holder.stl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]
2019-01-02 Led matrix using Raspi
2019-01-02 Led matrix using raspi
    Updated README
2019-01-02 Filling in the Alien Chest
    [arc_cup_holder.scad, arc_cup_holder.stl, arc_reactor.scad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]
2019-01-03 Minor modifications
    [arc_reactor.scad, head.scad]
2019-01-07 Model fn change, creating READMEs
    [arc_reactor_cup.scad, arm_left.scad, arm_right.scad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]
2019-01-09 Raspi 0 pin diagram
2019-01-10 LED Strip test with Raspi
    Code copied from https://learn.adafruit.com/neopixels-on-raspberry-pi/python-usage
2019-01-10 BL transfer from Raspi to Arduino Nano done
2019-01-11 Both way connection working!
    Bluetooth connect between Raspi and Arduino Nano with HC-05
2019-01-12 PowerHand module complete
    Basic testing done, Thorough testing required
2019-01-12 Update angle for gyro
2019-01-13 modified powerhand
2019-01-13 testing arduino to legs
2019-01-14 Version 3 model for Alien
    [Body.stl, arc_cup_holder.scad, arc_cup_holder.stl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]
2019-01-14 Correcting angle of elevation
    [backmost_hold.scad, backmost_hold.stl, base.scad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]
2019-01-14 testing eye in Arduino
2019-01-16 Adding the plexi model back
    [backmost_hold.scad]
2019-01-18 PowerHand model
    [battery_holder.scad, battery_holder.stl, bluetooth_holder.scad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]
2019-01-19 Enabling both LEDs(eyes)
2019-01-20 Translation gateway model
    [middle_part.scad, middle_part.stl, sonar_cut.scad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]
2019-01-21 LED testing code
2019-01-22 Added and updated emotions
    Added low power emotion and updated sleepy and sad emotions
2019-01-23 Models updated
    [Body.stl, arc_cup_holder.scad, arc_reactor.scad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]
2019-01-23 Changing the pin for LED Strip in powerhand
2019-01-23 Ground code - initial draft
2019-01-23 LED Strip PowerHand update
2019-01-24 Changing servo pins
2019-01-24 Pin description
2019-01-24 Led Strip pin
2019-01-25 Movement updates: pigpio and more
    alien/lib/README.md contains servo movement values
    updated eye_emotions delay to show emotions properly
    added movement2.0 with pigpio
    added gpio_controller
    updated servo values to be controlled from arduino too
    added pigpio test
2019-01-25 Ground code
2019-01-25 Setting up ground code
2019-01-26 LED Strip lighting
2019-01-28 Alien laser cuts
    [simple.stl, top.scad, top_part.scad]
2019-01-29 change in logic and some models
    [front.scad, top_part.scad]
2019-02-27 upload video powerhand
